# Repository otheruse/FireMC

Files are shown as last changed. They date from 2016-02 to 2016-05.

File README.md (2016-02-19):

 This is FireMC, a motion controller for RepRap 3D printers and Factory Robots like FirePick delta and others. FireMC is currently implemented as an Arduino Due add-on board. FireMC features:
- 12-30V input
- Separate heatbed input
- 12v 1.5A switching regulator for 12v peripherals (if input is not 12v)
- 7 pwm channels (1 heatbed, 3 high power, 1 med power and 2 channels connected to the 12v rail)
- Sockets for 6 stepper drivers
- micro-sd socket
- WiFi via esp8266 module
- 5 thermistor inputs
- 7 limit switch inputs
- 4 io's which can be used for thermocouple inputs and/or servos
- 2 expansion headers for LCD or other peripherals

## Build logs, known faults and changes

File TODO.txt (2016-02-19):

+ Input caps SMPS need 1206 footprint
+ R42 should not be 4K7 (probably 470R-1K)
+ Some motor connectors are too close to 100uF caps
+ Need a smaller inductor for SMPS
- Print info on silkscreen 
	+ jumper locations
	+ stepper name
	- stepper orientation
	+ connector name/function/polarity
+ Via's in power tracks should be bigger (or multiple via's)
+ Check if SMPS is working/what is wrong
+ check what we have on d13 - has arduino led on it
- See if it's useful to connect more IO's of the esp8266 to the arduino
+ Check if we can have hardware PWM on some (all?) of the pwm outputs (pwm outputs are d2-d13) -> We now have all except LP-FET2 on pwm outputs
+ Don't use tx0 and rx0, they are connected to the atmega 16u2
+ pin 20 and 21 (sda and scl) have 1k5 pull-ups: check what's connected to them! -> Now: eeprom
+ is the led on a high-current pin? -> No. Is on the same pin as arduino led
+ Add header for I2C (sda, scl and gnd)
+ Add 5v, GND, SIG for Karl

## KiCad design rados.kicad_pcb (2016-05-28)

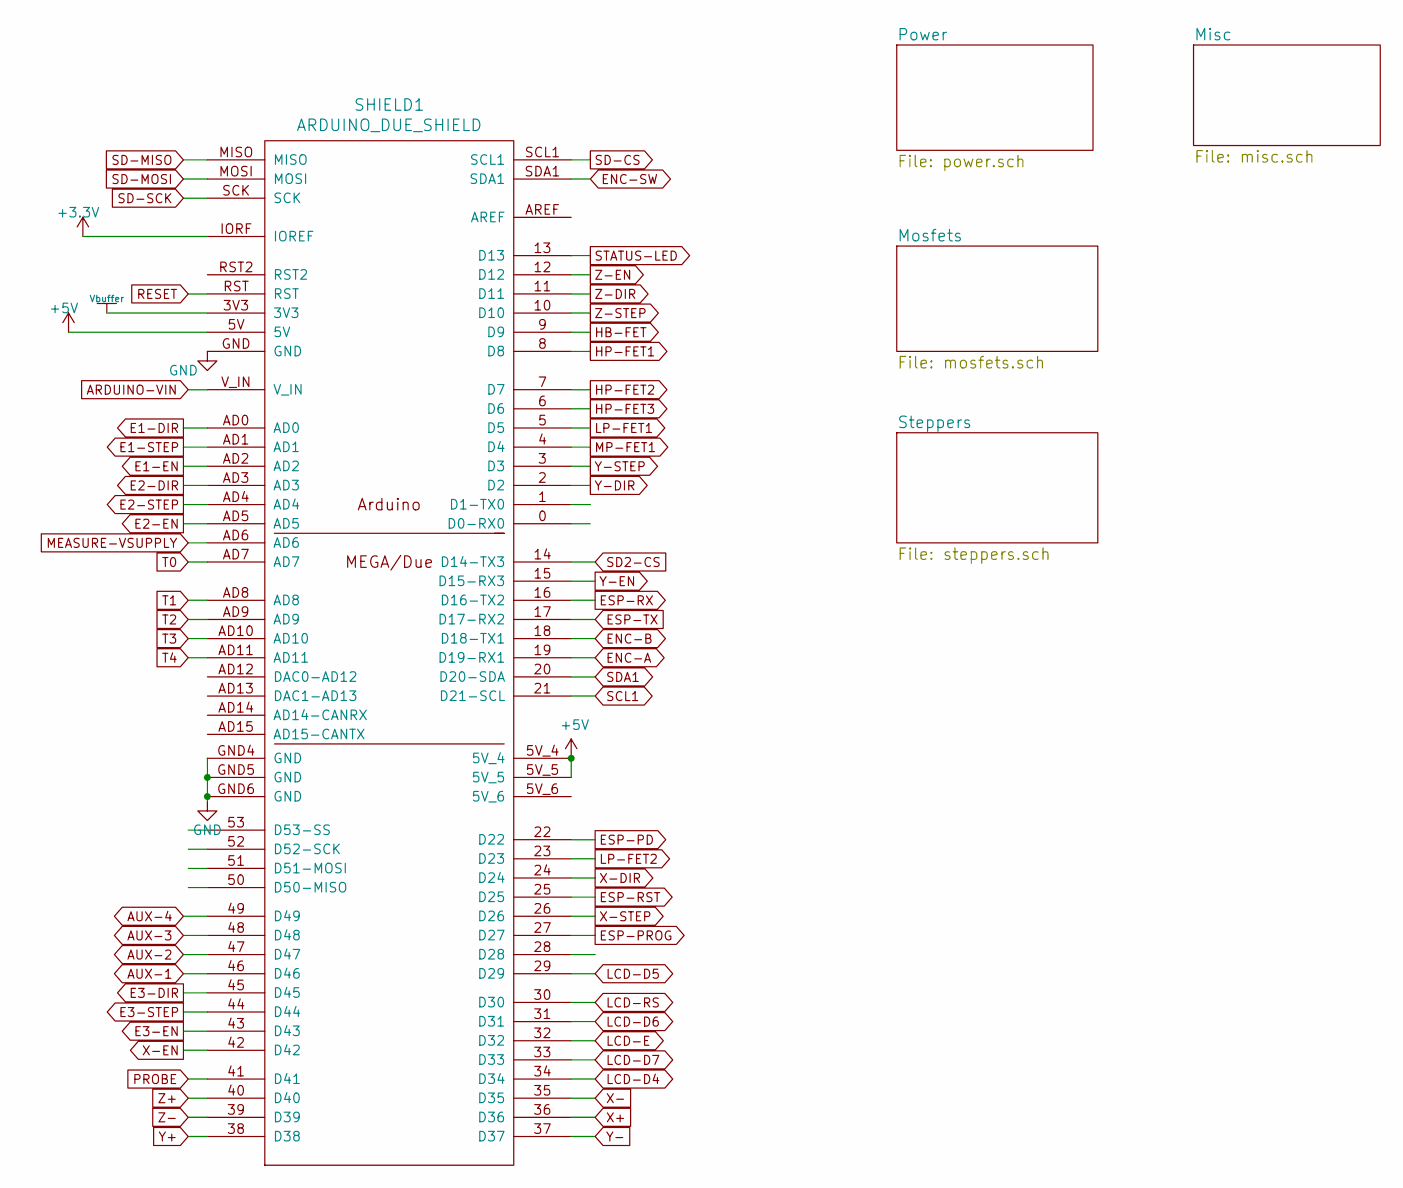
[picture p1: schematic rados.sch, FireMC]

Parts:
SHIELD1: ARDUINO_DUE_SHIELD; ARDUINO_MEGA_DUE_SHIELD_FOOTPRINT_OTH2

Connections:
+5V: SHIELD1.5V, SHIELD1.5V_4, SHIELD1.5V_5; also elsewhere on the board
ARDUINO-VIN: SHIELD1.V_IN; also elsewhere on the board
AUX-1: SHIELD1.46 (D46); also elsewhere on the board
AUX-2: SHIELD1.47 (D47); also elsewhere on the board
AUX-3: SHIELD1.48 (D48); also elsewhere on the board
AUX-4: SHIELD1.49 (D49); also elsewhere on the board
E1-DIR: SHIELD1.AD0; also elsewhere on the board
E1-EN: SHIELD1.AD2; also elsewhere on the board
E1-STEP: SHIELD1.AD1; also elsewhere on the board
E2-DIR: SHIELD1.AD3; also elsewhere on the board
E2-EN: SHIELD1.AD5; also elsewhere on the board
E2-STEP: SHIELD1.AD4; also elsewhere on the board
E3-DIR: SHIELD1.45 (D45); also elsewhere on the board
E3-EN: SHIELD1.43 (D43); also elsewhere on the board
E3-STEP: SHIELD1.44 (D44); also elsewhere on the board
ENC-A: SHIELD1.19 (D19-RX1); also elsewhere on the board
ENC-B: SHIELD1.18 (D18-TX1); also elsewhere on the board
ENC-SW: SHIELD1.SDA1; also elsewhere on the board
ESP-PD: SHIELD1.22 (D22); also elsewhere on the board
ESP-PROG: SHIELD1.27 (D27); also elsewhere on the board
ESP-RST: SHIELD1.25 (D25); also elsewhere on the board
ESP-RX: SHIELD1.16 (D16-TX2); also elsewhere on the board
ESP-TX: SHIELD1.17 (D17-RX2); also elsewhere on the board
GND: SHIELD1.GND, SHIELD1.GND4 (GND), SHIELD1.GND5 (GND), SHIELD1.GND6 (GND); also elsewhere on the board
HB-FET: SHIELD1.9 (D9); also elsewhere on the board
HP-FET1: SHIELD1.8 (D8); also elsewhere on the board
HP-FET2: SHIELD1.7 (D7); also elsewhere on the board
HP-FET3: SHIELD1.6 (D6); also elsewhere on the board
LCD-D4: SHIELD1.34 (D34); also elsewhere on the board
LCD-D5: SHIELD1.29 (D29); also elsewhere on the board
LCD-D6: SHIELD1.31 (D31); also elsewhere on the board
LCD-D7: SHIELD1.33 (D33); also elsewhere on the board
LCD-E: SHIELD1.32 (D32); also elsewhere on the board
LCD-RS: SHIELD1.30 (D30); also elsewhere on the board
LP-FET1: SHIELD1.5 (D5); also elsewhere on the board
LP-FET2: SHIELD1.23 (D23); also elsewhere on the board
MEASURE-VSUPPLY: SHIELD1.AD6; also elsewhere on the board
MP-FET1: SHIELD1.4 (D4); also elsewhere on the board
PROBE: SHIELD1.41 (D41); also elsewhere on the board
RESET: SHIELD1.RST; also elsewhere on the board
SCL1: SHIELD1.21 (D21-SCL); also elsewhere on the board
SD2-CS: SHIELD1.14 (D14-TX3); also elsewhere on the board
SD-CS: SHIELD1.SCL1; also elsewhere on the board
SD-MISO: SHIELD1.MISO; also elsewhere on the board
SD-MOSI: SHIELD1.MOSI; also elsewhere on the board
SD-SCK: SHIELD1.SCK; also elsewhere on the board
SDA1: SHIELD1.20 (D20-SDA); also elsewhere on the board
STATUS-LED: SHIELD1.13 (D13); also elsewhere on the board
T0: SHIELD1.AD7; also elsewhere on the board
T1: SHIELD1.AD8; also elsewhere on the board
T2: SHIELD1.AD9; also elsewhere on the board
T3: SHIELD1.AD10; also elsewhere on the board
T4: SHIELD1.AD11; also elsewhere on the board
Vbuffer: SHIELD1.3V3
X+: SHIELD1.36 (D36); also elsewhere on the board
X-: SHIELD1.35 (D35); also elsewhere on the board
X-DIR: SHIELD1.24 (D24); also elsewhere on the board
X-EN: SHIELD1.42 (D42); also elsewhere on the board
X-STEP: SHIELD1.26 (D26); also elsewhere on the board
Y+: SHIELD1.38 (D38); also elsewhere on the board
Y-: SHIELD1.37 (D37); also elsewhere on the board
Y-DIR: SHIELD1.2 (D2); also elsewhere on the board
Y-EN: SHIELD1.15 (D15-RX3); also elsewhere on the board
Y-STEP: SHIELD1.3 (D3); also elsewhere on the board
Z+: SHIELD1.40 (D40); also elsewhere on the board
Z-: SHIELD1.39 (D39); also elsewhere on the board
Z-DIR: SHIELD1.11 (D11); also elsewhere on the board
Z-EN: SHIELD1.12 (D12); also elsewhere on the board
Z-STEP: SHIELD1.10 (D10); also elsewhere on the board

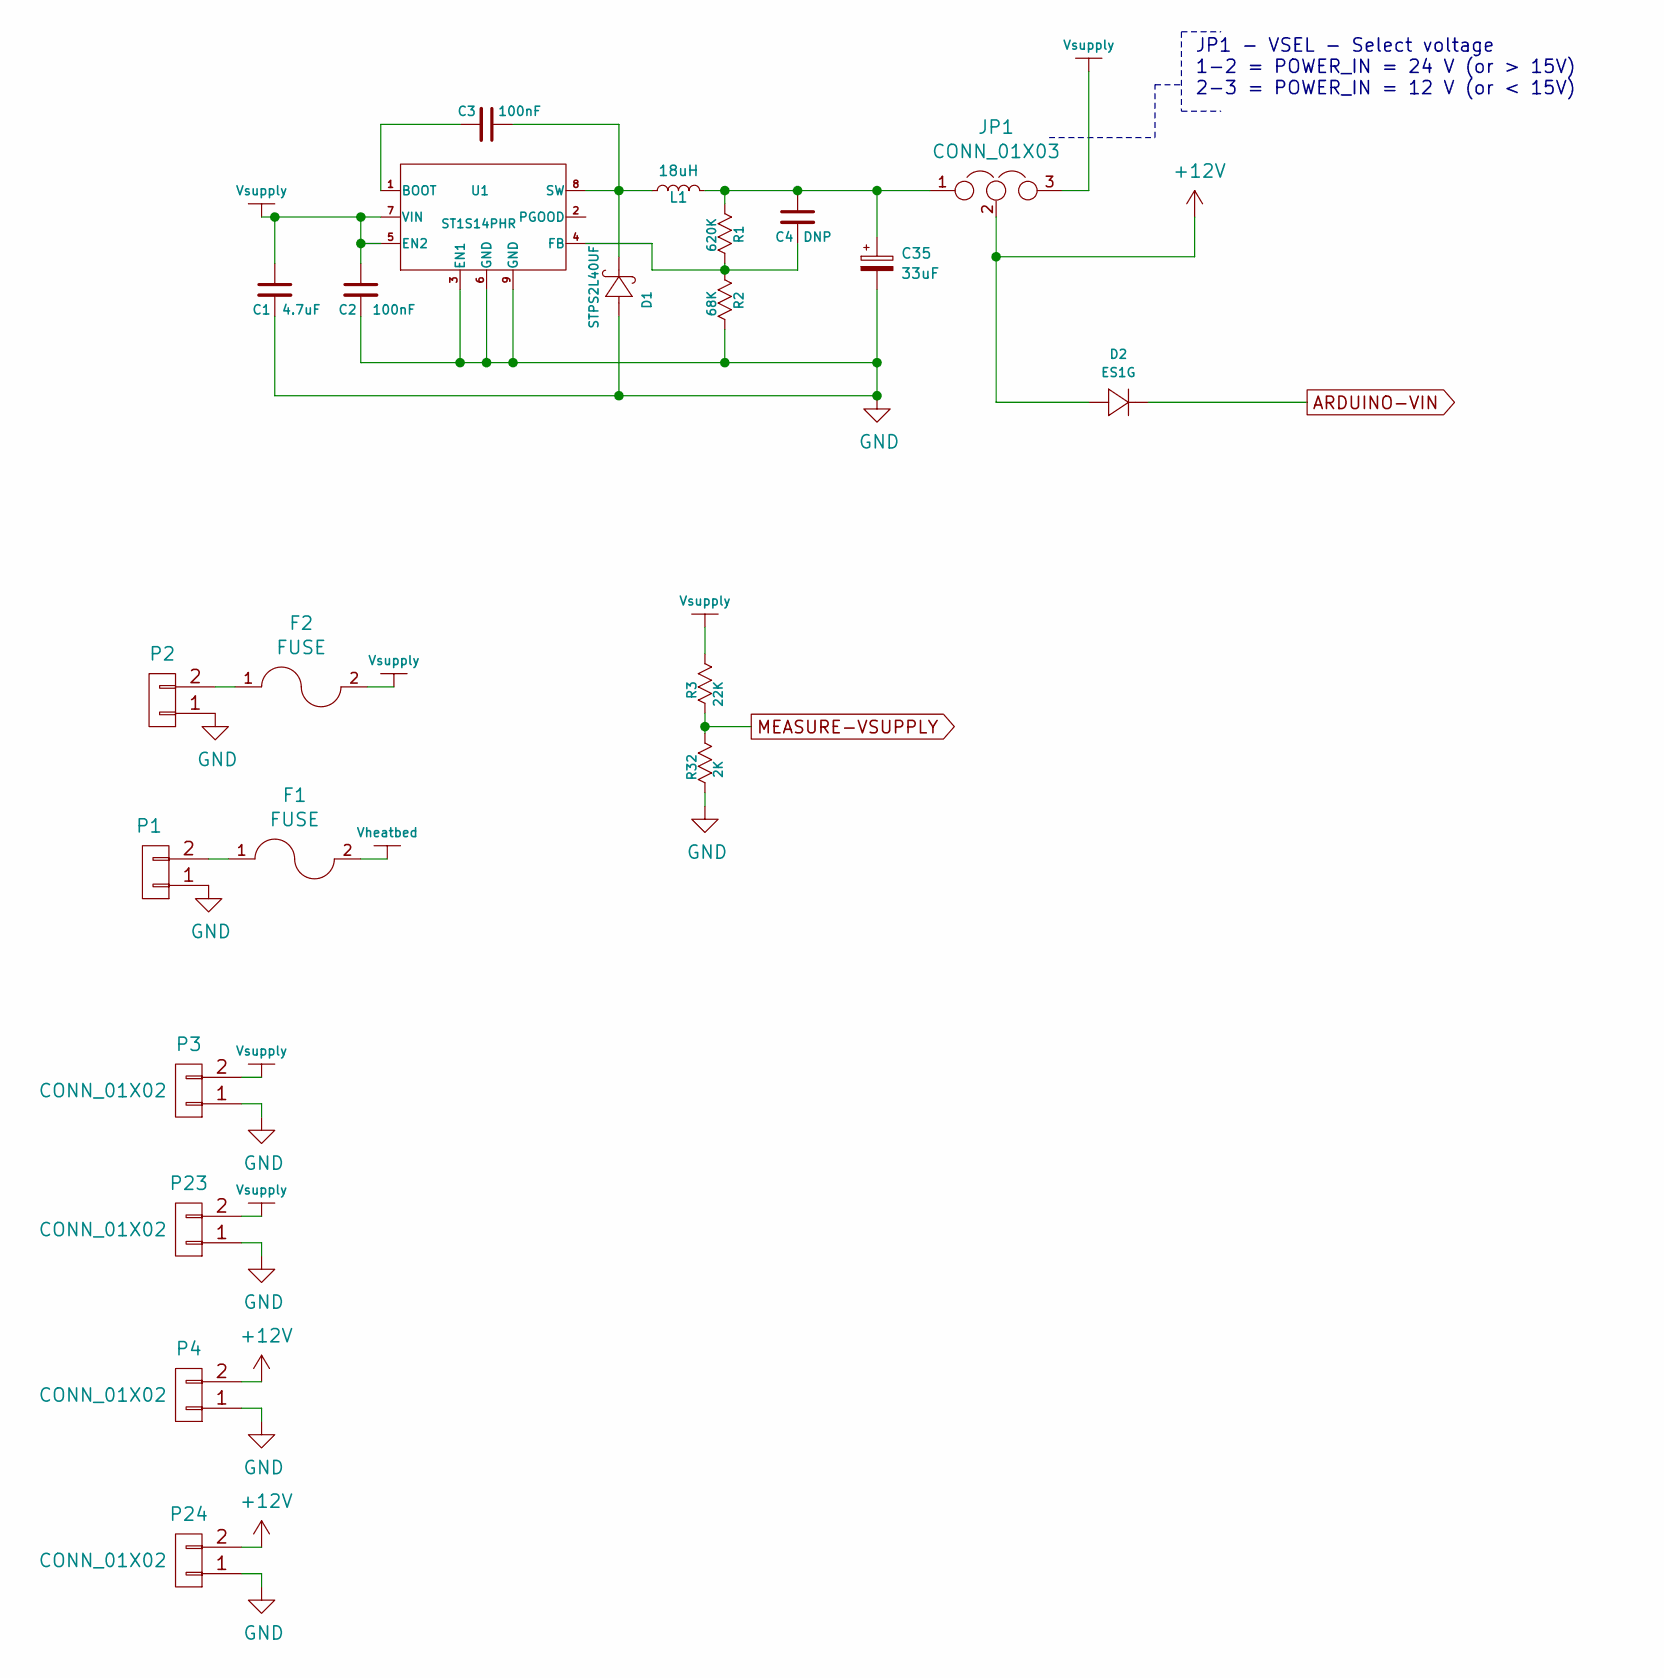
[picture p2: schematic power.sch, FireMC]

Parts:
C1: 4.7uF; C_1210; VoltageRating 50V
C2, C3: 100nF; C_0603; VoltageRating 50V
C4: DNP; C_0603
C35: 33uF; c_elec_6.3x7.7; VoltageRating 25V
D1: STPS2L40UF; DO214AA_SMB
D2: ES1G; DO214AC_SMA
F1, F2: FUSE; FUSEHOLDER_MINI_KEYSTONE_3557
JP1: CONN_01X03; CON_HDR_1x3_2.54mm
L1: 18uH; INDUCTOR_BOURNS_RLB914
P1, P2: CONN_01X02; CON_PHOENIX_MSTBA-2.5-2-G-5.08
P3, P4, P23, P24: CONN_01X02; CON_HDR_1x2_2.54mm
R1: 620K; R_0603
R2: 68K; R_0603
R3: 22K; R_0603
R32: 2K; R_0603
U1: ST1S14PHR; HSOP8

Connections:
+12V: D2.2, JP1.2, P4.2, P24.2; also elsewhere on the board
GND: C1.2, C2.2, C35.2, D1.2 (anode), P1.1, P2.1, P3.1, P4.1, P23.1, P24.1, R2.2, R32.2, U1.3 (EN1), U1.6 (GND), U1.9 (GND); also elsewhere on the board
MEASURE-VSUPPLY: R3.2, R32.1; also elsewhere on the board
unnamed: C3.1, D1.1 (cathode), L1.1, U1.8 (SW)
unnamed: C3.2, U1.1 (BOOT)
unnamed: C4.2, R1.2, R2.1, U1.4 (FB)
unnamed: C4.1, C35.1, JP1.1, L1.2, R1.1
unnamed 50: D2.1; also elsewhere on the board
unnamed: F1.1, P1.2
unnamed: F2.1, P2.2
Vheatbed: F1.2; also elsewhere on the board
Vsupply: C1.1, C2.1, F2.2, JP1.3, P3.2, P23.2, R3.1, U1.5 (EN2), U1.7 (VIN); also elsewhere on the board

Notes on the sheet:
JP1 - VSEL - Select voltage 1-2 = POWER_IN = 24 V (or > 15V) 2-3 = POWER_IN = 12 V (or < 15V)

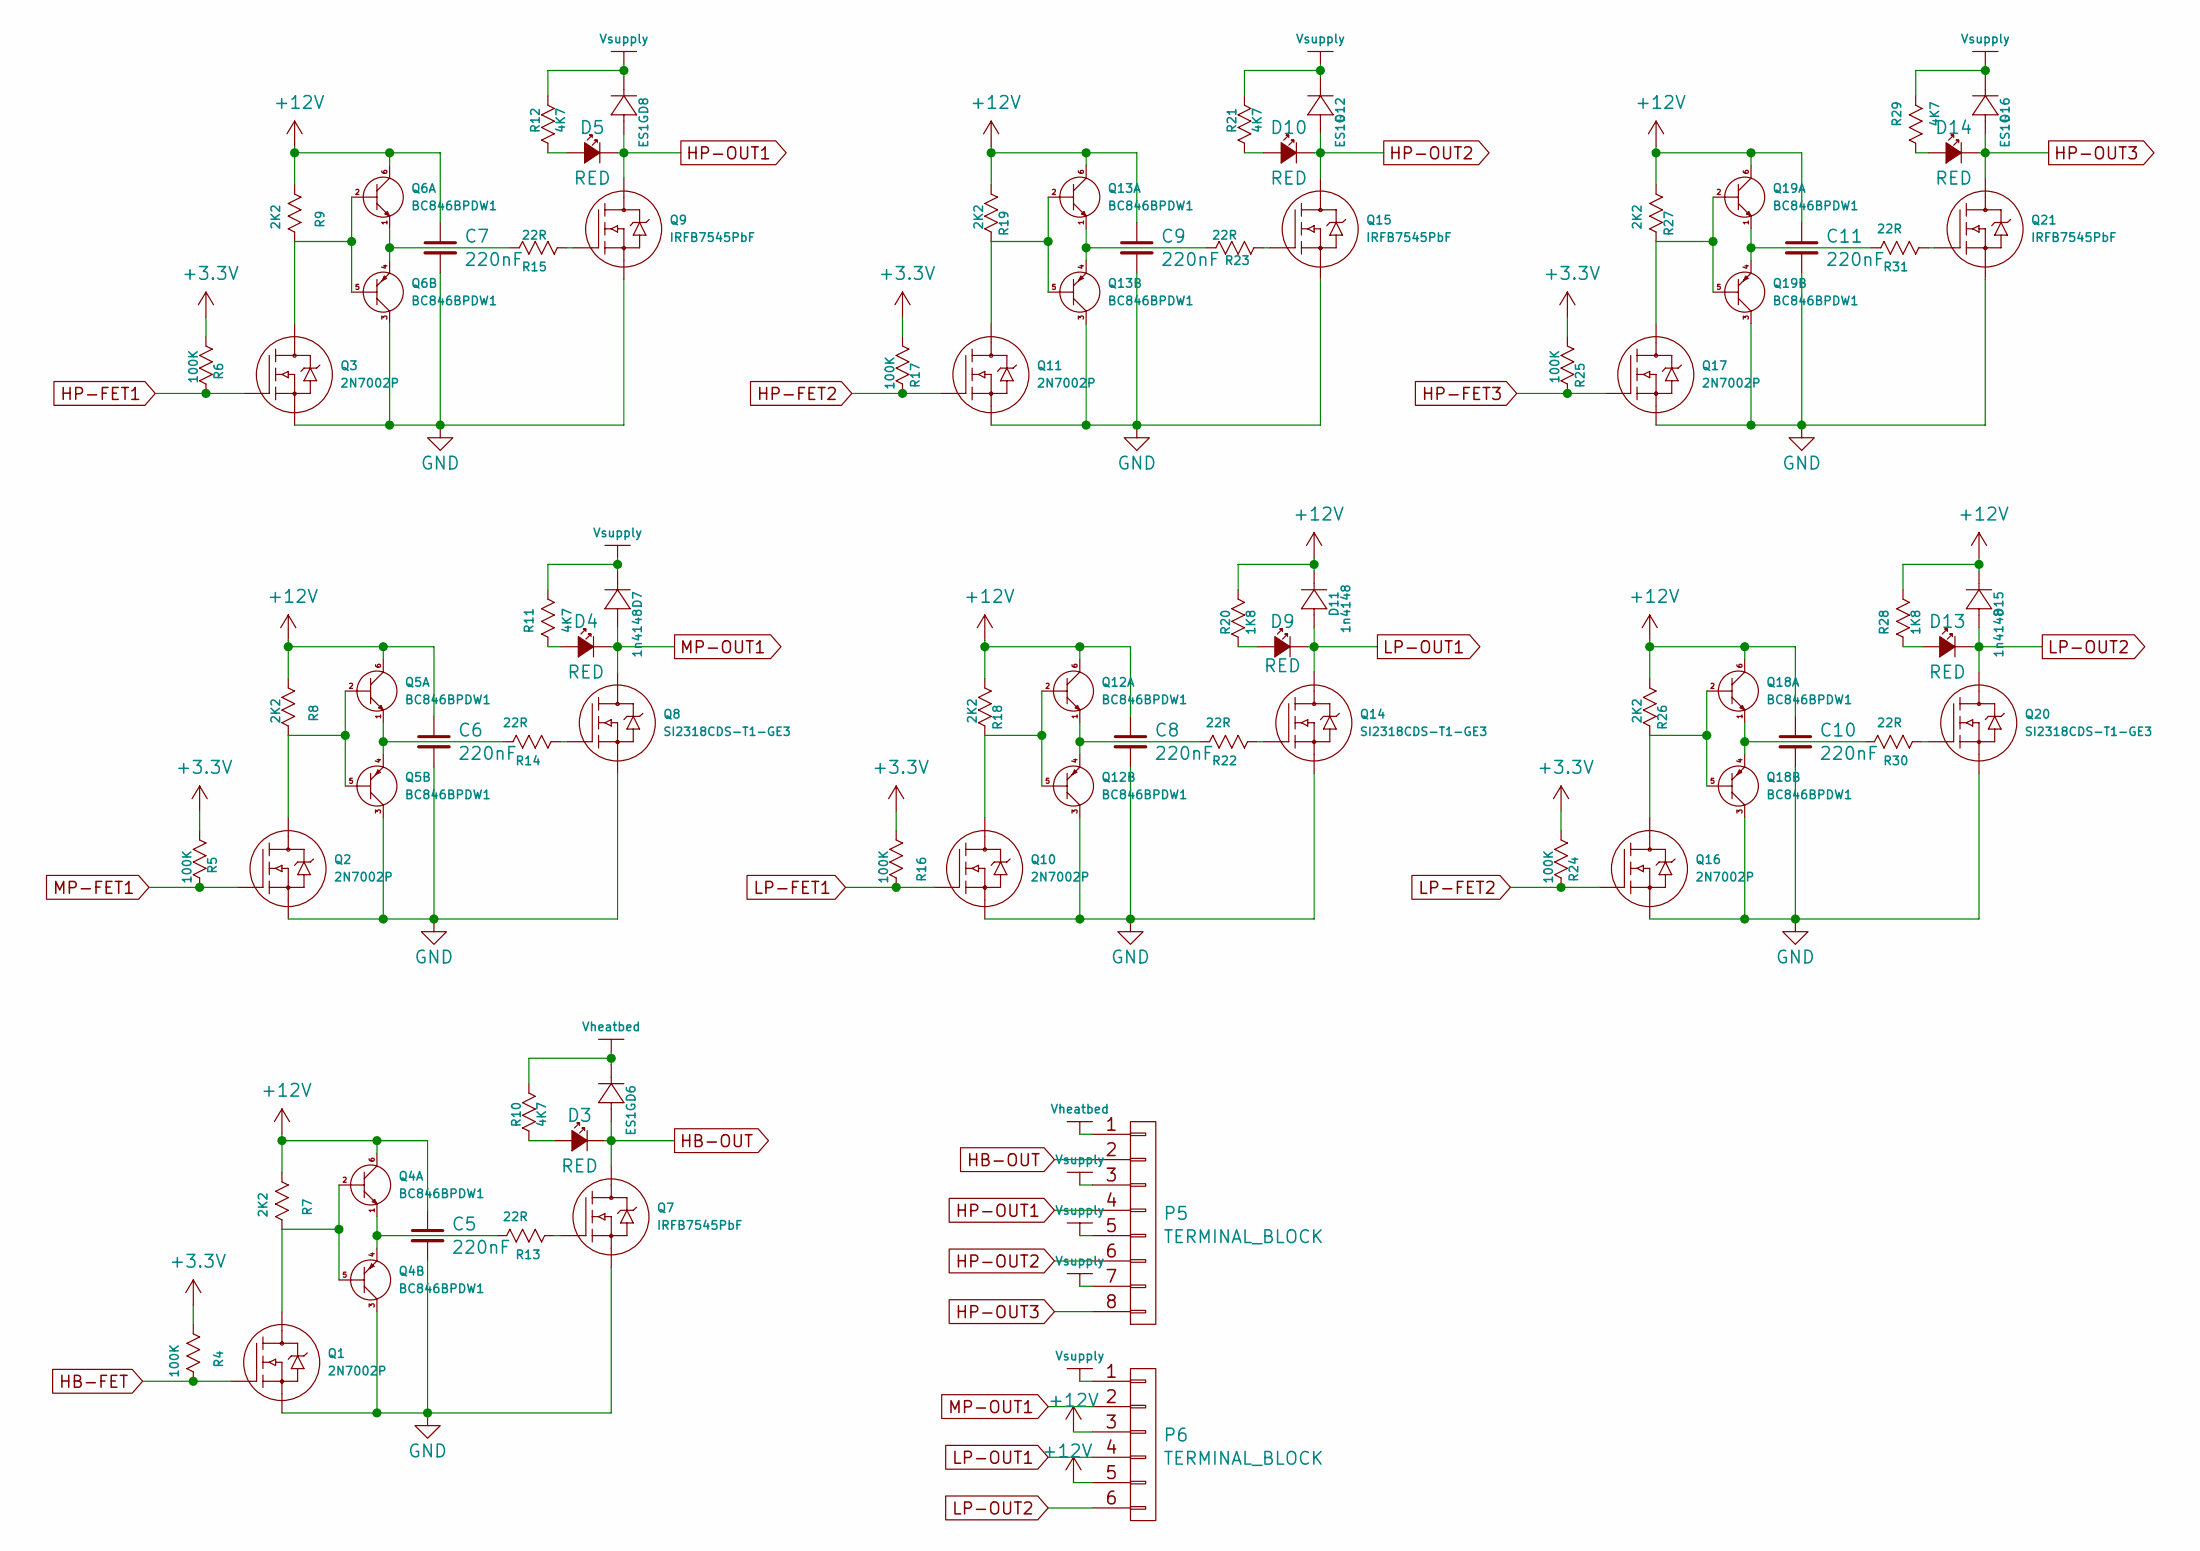
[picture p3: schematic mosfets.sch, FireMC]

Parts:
C5, C6, C7, C8, C9, C10, C11: 220nF; C_0603; VoltageRating 16V
D3, D4, D5, D9, D10, D13, D14: RED; LED-0603
D6, D8, D12, D16: ES1G; DO214AC_SMA
D7, D11, D15: 1n4148; DO213AA_SOD-80_MiniMelf
P5: TERMINAL_BLOCK; TERMINAL_BLOCK_8_PIN_5mm
P6: TERMINAL_BLOCK; TERMINAL_BLOCK_6_PIN_5mm
Q1, Q2, Q3, Q10, Q11, Q16, Q17: 2N7002P; SOT23_3L
Q4, Q5, Q6, Q12, Q13, Q18, Q19: BC846BPDW1; SC70_6L
Q7, Q9, Q15, Q21: IRFB7545PbF; TO-220-3
Q8, Q14, Q20: SI2318CDS-T1-GE3; SOT23_3L
R4, R5, R6, R16, R17, R24, R25: 100K; R_0603
R7, R8, R9, R18, R19, R26, R27: 2K2; R_0603
R10, R11, R12, R21, R29: 4K7; R_0805
R13, R14, R15, R22, R23, R30, R31: 22R; R_0603
R20, R28: 1K8; R_0603

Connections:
+12V: C5.1, C6.1, C7.1, C8.1, C9.1, C10.1, C11.1, D11.2, D15.2, P6.3, P6.5, Q4.6 (C), Q5.6 (C), Q6.6 (C), Q12.6 (C), Q13.6 (C), Q18.6 (C), Q19.6 (C), R7.2, R8.2, R9.2, R18.2, R19.2, R20.1, R26.2, R27.2, R28.1; also elsewhere on the board
GND: C5.2, C6.2, C7.2, C8.2, C9.2, C10.2, C11.2, Q1.2 (S), Q2.2 (S), Q3.2 (S), Q4.3 (C), Q5.3 (C), Q6.3 (C), Q7.3 (S), Q8.2 (S), Q9.3 (S), Q10.2 (S), Q11.2 (S), Q12.3 (C), Q13.3 (C), Q14.2 (S), Q15.3 (S), Q16.2 (S), Q17.2 (S), Q18.3 (C), Q19.3 (C), Q20.2 (S), Q21.3 (S); also elsewhere on the board
HB-FET: Q1.1 (G), R4.1; also elsewhere on the board
HB-OUT: D3.2 (K), D6.2, P5.2, Q7.2 (D)
HP-FET1: Q3.1 (G), R6.1; also elsewhere on the board
HP-FET2: Q11.1 (G), R17.1; also elsewhere on the board
HP-FET3: Q17.1 (G), R25.1; also elsewhere on the board
HP-OUT1: D5.2 (K), D8.2, P5.4, Q9.2 (D)
HP-OUT2: D10.2 (K), D12.2, P5.6, Q15.2 (D)
HP-OUT3: D14.2 (K), D16.2, P5.8, Q21.2 (D)
LP-FET1: Q10.1 (G), R16.1; also elsewhere on the board
LP-FET2: Q16.1 (G), R24.1; also elsewhere on the board
LP-OUT1: D9.2 (K), D11.1, P6.4, Q14.3 (D)
LP-OUT2: D13.2 (K), D15.1, P6.6, Q20.3 (D)
MP-FET1: Q2.1 (G), R5.1; also elsewhere on the board
MP-OUT1: D4.2 (K), D7.1, P6.2, Q8.3 (D)
unnamed: D3.1 (A), R10.2
unnamed: D4.1 (A), R11.2
unnamed: D5.1 (A), R12.2
unnamed: D9.1 (A), R20.2
unnamed: D10.1 (A), R21.2
unnamed: D13.1 (A), R28.2
unnamed: D14.1 (A), R29.2
unnamed: Q1.3 (D), Q4.2 (B), Q4.5 (B), R7.1
unnamed: Q2.3 (D), Q5.2 (B), Q5.5 (B), R8.1
unnamed: Q3.3 (D), Q6.2 (B), Q6.5 (B), R9.1
unnamed: Q4.1 (E), Q4.4 (E), R13.1
unnamed: Q5.1 (E), Q5.4 (E), R14.1
unnamed: Q6.1 (E), Q6.4 (E), R15.1
unnamed: Q7.1 (G), R13.2
unnamed: Q8.1 (G), R14.2
unnamed: Q9.1 (G), R15.2
unnamed: Q10.3 (D), Q12.2 (B), Q12.5 (B), R18.1
unnamed: Q11.3 (D), Q13.2 (B), Q13.5 (B), R19.1
unnamed: Q12.1 (E), Q12.4 (E), R22.1
unnamed: Q13.1 (E), Q13.4 (E), R23.1
unnamed: Q14.1 (G), R22.2
unnamed: Q15.1 (G), R23.2
unnamed: Q16.3 (D), Q18.2 (B), Q18.5 (B), R26.1
unnamed: Q17.3 (D), Q19.2 (B), Q19.5 (B), R27.1
unnamed: Q18.1 (E), Q18.4 (E), R30.1
unnamed: Q19.1 (E), Q19.4 (E), R31.1
unnamed: Q20.1 (G), R30.2
unnamed: Q21.1 (G), R31.2
Vheatbed: D6.1, P5.1, R10.1; also elsewhere on the board
Vsupply: D7.2, D8.1, D12.1, D16.1, P5.3, P5.5, P5.7, P6.1, R11.1, R12.1, R21.1, R29.1; also elsewhere on the board

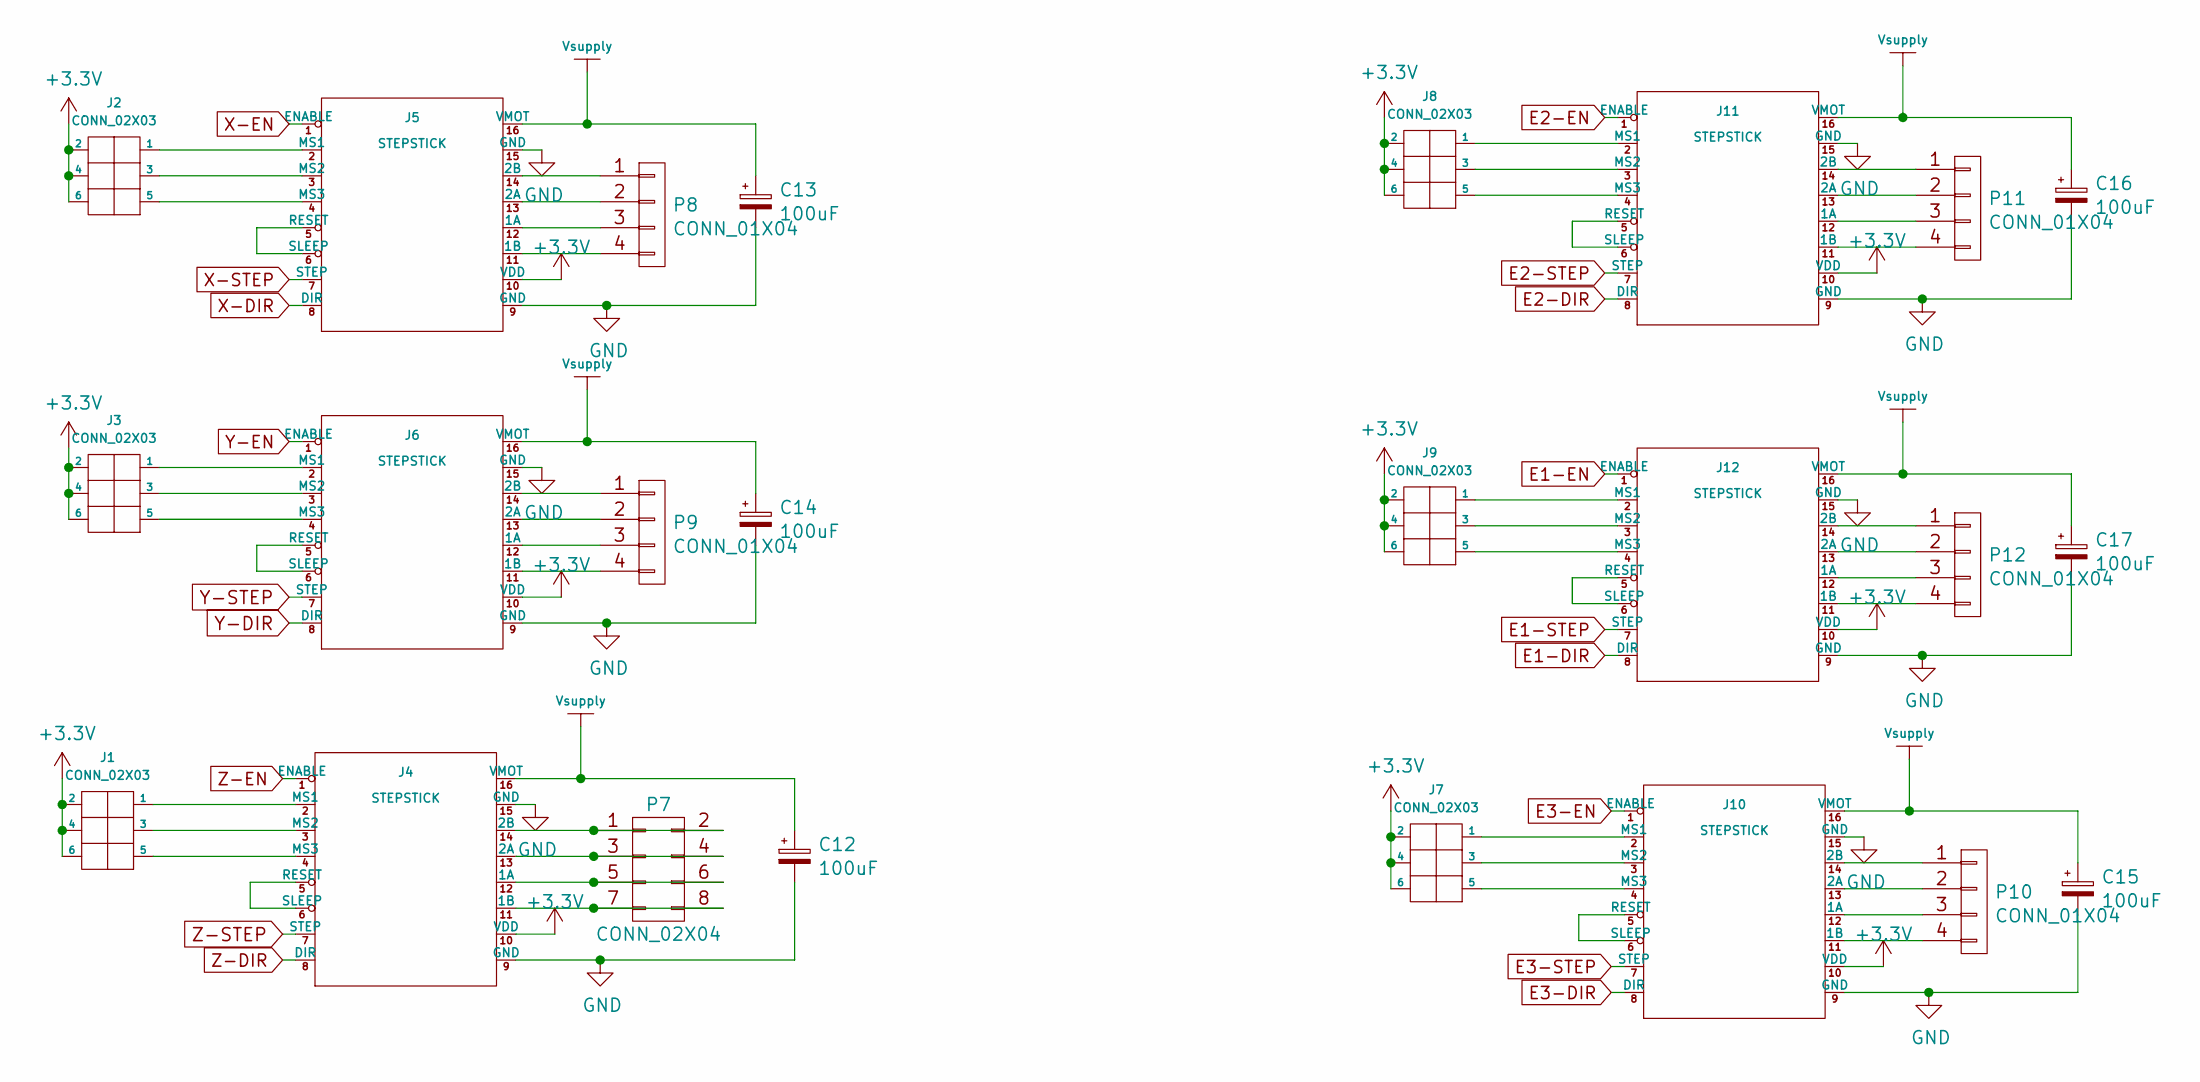
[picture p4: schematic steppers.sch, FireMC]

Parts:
C12, C13, C14, C15, C16, C17: 100uF; c_elec_6.3x7.7; VoltageRating 50V
J1, J2, J3, J7, J8, J9: CONN_02X03; CON_HDR_2x3_2.54mm
J4, J5, J6, J10, J11, J12: STEPSTICK
P7: CONN_02X04; CON_HDR_2x4_2.54mm
P8, P9, P10, P11, P12: CONN_01X04; CON_HDR_1x4_2.54mm

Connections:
E1-DIR: J12.8 (DIR); also elsewhere on the board
E1-EN: J12.1 (ENABLE); also elsewhere on the board
E1-STEP: J12.7 (STEP); also elsewhere on the board
E2-DIR: J11.8 (DIR); also elsewhere on the board
E2-EN: J11.1 (ENABLE); also elsewhere on the board
E2-STEP: J11.7 (STEP); also elsewhere on the board
E3-DIR: J10.8 (DIR); also elsewhere on the board
E3-EN: J10.1 (ENABLE); also elsewhere on the board
E3-STEP: J10.7 (STEP); also elsewhere on the board
GND: C12.2, C13.2, C14.2, C15.2, C16.2, C17.2, J4.9 (GND), J4.15 (GND), J5.9 (GND), J5.15 (GND), J6.9 (GND), J6.15 (GND), J10.9 (GND), J10.15 (GND), J11.9 (GND), J11.15 (GND), J12.9 (GND), J12.15 (GND); also elsewhere on the board
unnamed: J1.1, J4.2 (MS1)
unnamed: J1.3, J4.3 (MS2)
unnamed: J1.5, J4.4 (MS3)
unnamed: J2.1, J5.2 (MS1)
unnamed: J2.3, J5.3 (MS2)
unnamed: J2.5, J5.4 (MS3)
unnamed: J3.1, J6.2 (MS1)
unnamed: J3.3, J6.3 (MS2)
unnamed: J3.5, J6.4 (MS3)
unnamed: J4.5 (RESET), J4.6 (SLEEP)
unnamed: J4.11 (1B), P7.7, P7.8
unnamed: J4.12 (1A), P7.5, P7.6
unnamed: J4.13 (2A), P7.3, P7.4
unnamed: J4.14 (2B), P7.1, P7.2
unnamed: J5.5 (RESET), J5.6 (SLEEP)
unnamed: J5.11 (1B), P8.4
unnamed: J5.12 (1A), P8.3
unnamed: J5.13 (2A), P8.2
unnamed: J5.14 (2B), P8.1
unnamed: J6.5 (RESET), J6.6 (SLEEP)
unnamed: J6.11 (1B), P9.4
unnamed: J6.12 (1A), P9.3
unnamed: J6.13 (2A), P9.2
unnamed: J6.14 (2B), P9.1
unnamed: J7.1, J10.2 (MS1)
unnamed: J7.3, J10.3 (MS2)
unnamed: J7.5, J10.4 (MS3)
unnamed: J10.5 (RESET), J10.6 (SLEEP)
unnamed: J10.11 (1B), P10.4
unnamed: J10.12 (1A), P10.3
unnamed: J10.13 (2A), P10.2
unnamed: J10.14 (2B), P10.1
unnamed: J8.1, J11.2 (MS1)
unnamed: J8.3, J11.3 (MS2)
unnamed: J8.5, J11.4 (MS3)
unnamed: J11.5 (RESET), J11.6 (SLEEP)
unnamed: J11.11 (1B), P11.4
unnamed: J11.12 (1A), P11.3
unnamed: J11.13 (2A), P11.2
unnamed: J11.14 (2B), P11.1
unnamed: J9.1, J12.2 (MS1)
unnamed: J9.3, J12.3 (MS2)
unnamed: J9.5, J12.4 (MS3)
unnamed: J12.5 (RESET), J12.6 (SLEEP)
unnamed: J12.11 (1B), P12.4
unnamed: J12.12 (1A), P12.3
unnamed: J12.13 (2A), P12.2
unnamed: J12.14 (2B), P12.1
Vsupply: C12.1, C13.1, C14.1, C15.1, C16.1, C17.1, J4.16 (VMOT), J5.16 (VMOT), J6.16 (VMOT), J10.16 (VMOT), J11.16 (VMOT), J12.16 (VMOT); also elsewhere on the board
X-DIR: J5.8 (DIR); also elsewhere on the board
X-EN: J5.1 (ENABLE); also elsewhere on the board
X-STEP: J5.7 (STEP); also elsewhere on the board
Y-DIR: J6.8 (DIR); also elsewhere on the board
Y-EN: J6.1 (ENABLE); also elsewhere on the board
Y-STEP: J6.7 (STEP); also elsewhere on the board
Z-DIR: J4.8 (DIR); also elsewhere on the board
Z-EN: J4.1 (ENABLE); also elsewhere on the board
Z-STEP: J4.7 (STEP); also elsewhere on the board

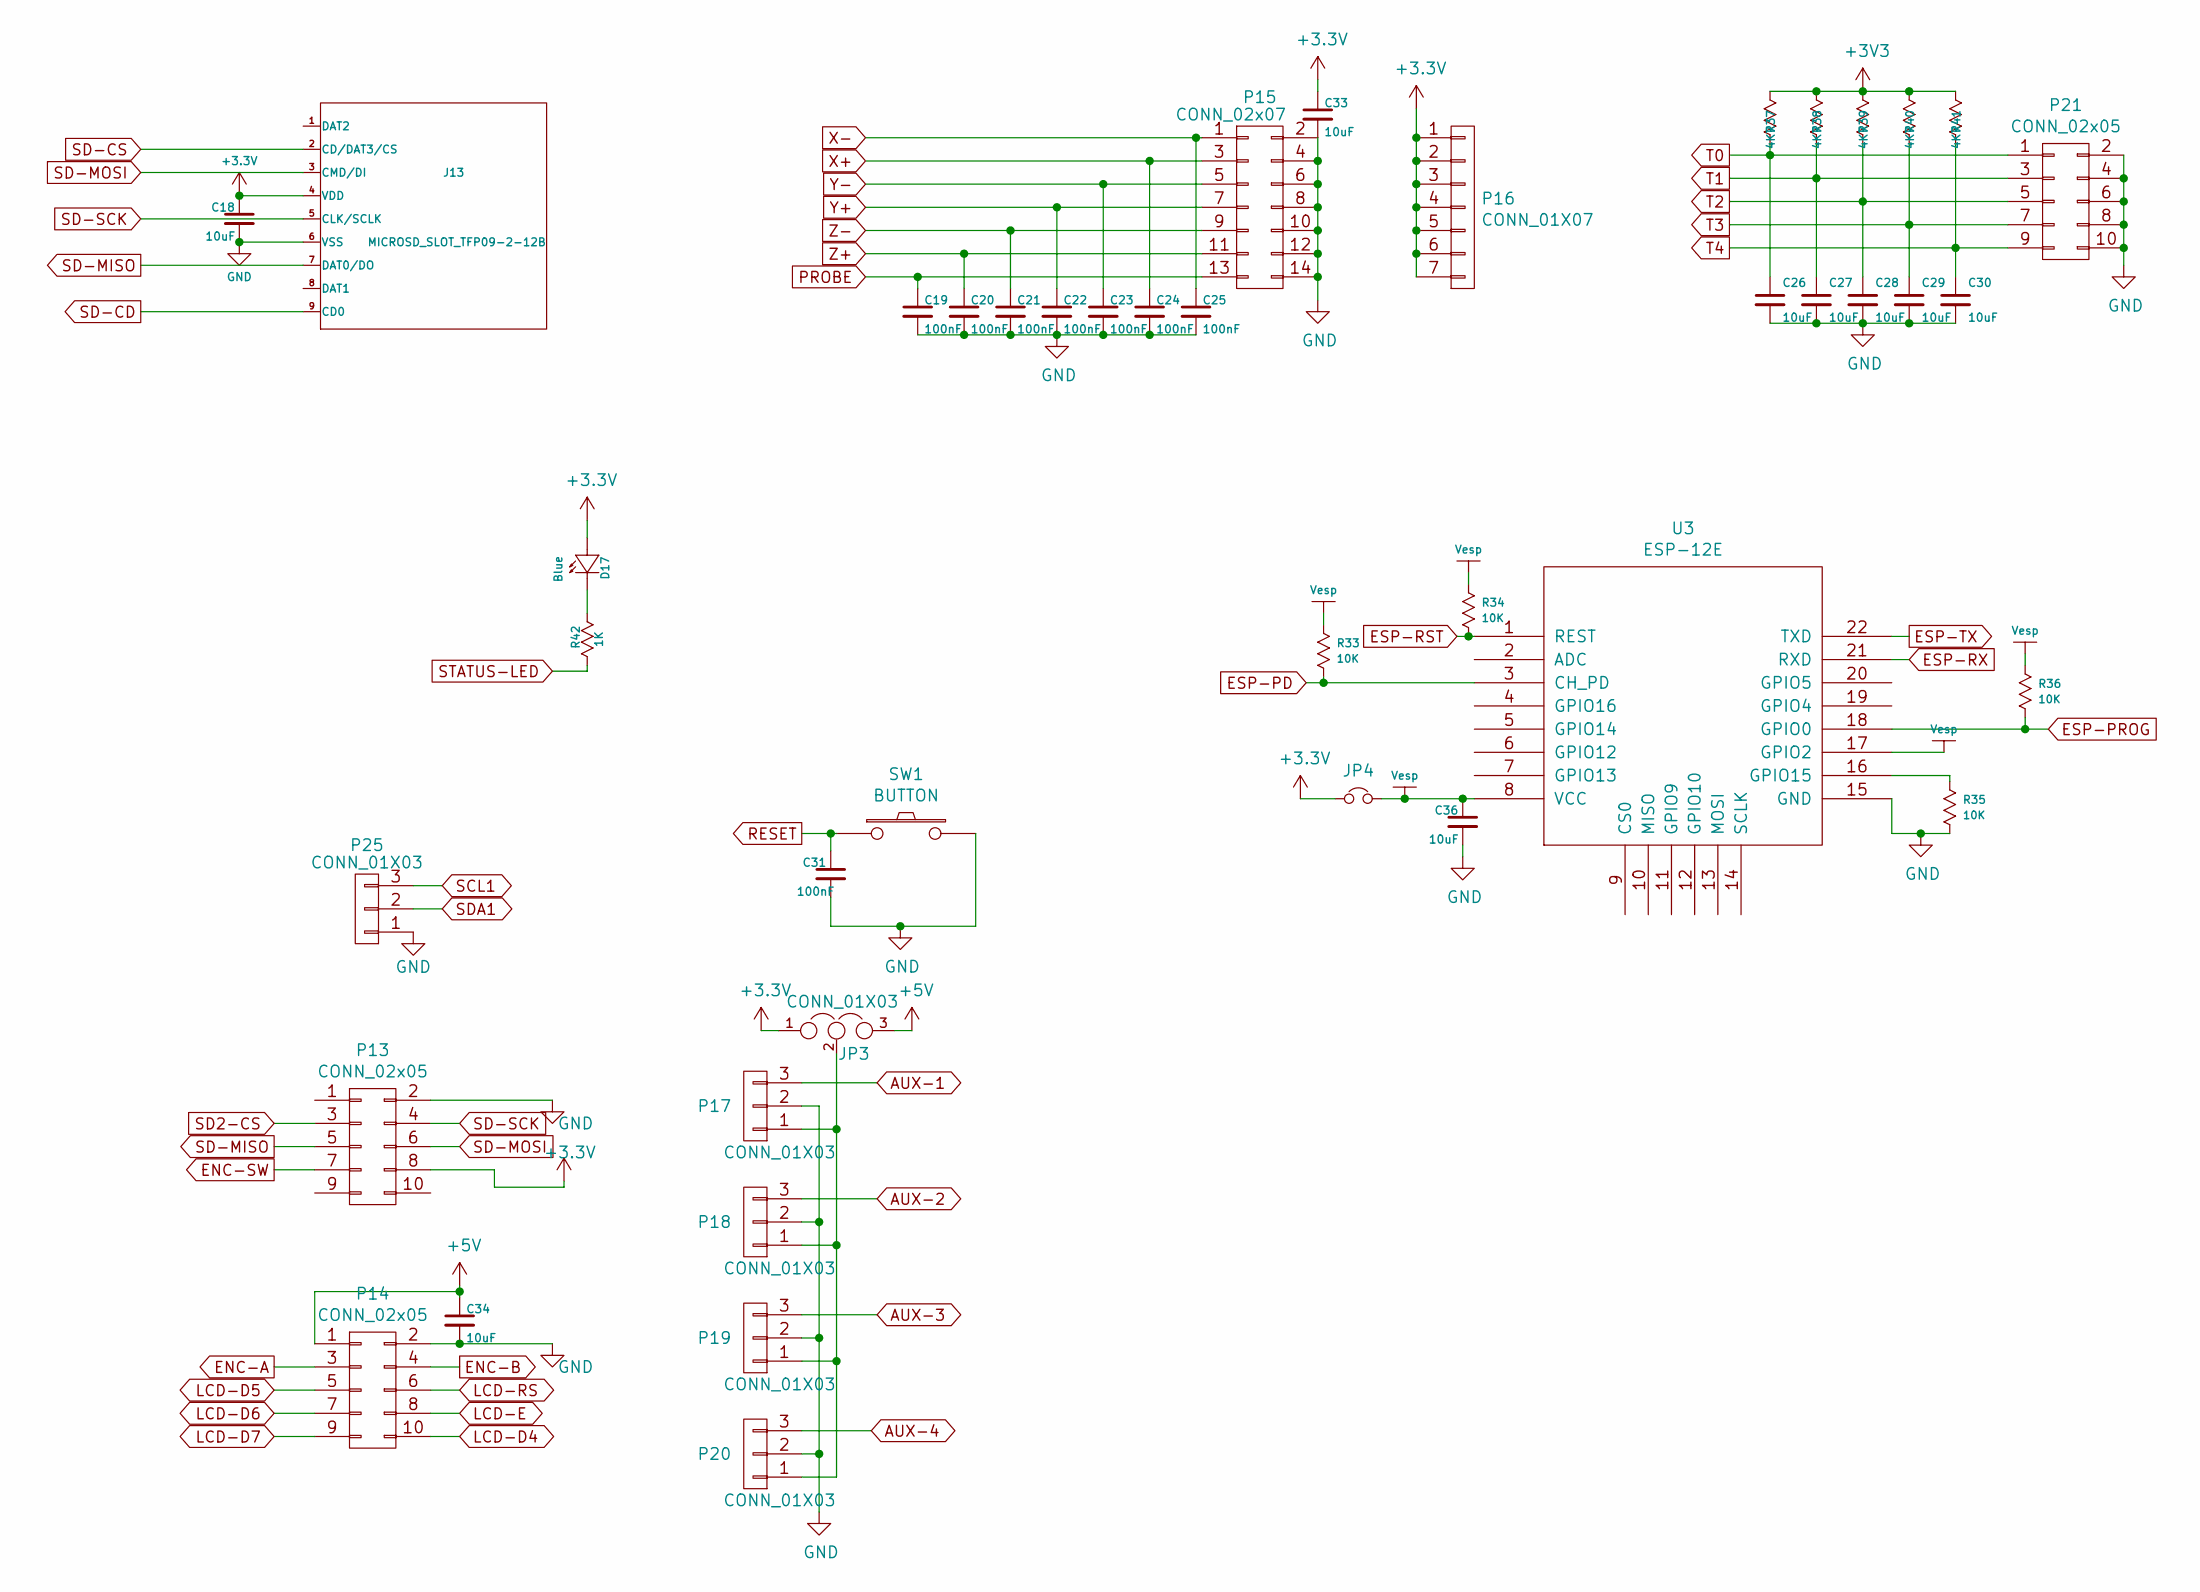
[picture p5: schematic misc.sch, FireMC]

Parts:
C18, C26, C27, C28, C29, C30, C33, C34, C36: 10uF; C_0805; VoltageRating 6.3V
C19, C20, C21, C22, C23, C24, C25, C31: 100nF; C_0603; VoltageRating 16V
D17: Blue; LED-0603
J13: MICROSD_SLOT_TFP09-2-12B
JP3: CONN_01X03; CON_HDR_1x3_2.54mm
JP4: CONN_01X02; CON_HDR_1x2_2.54mm
P13, P14, P21: CONN_02x05; CON_HDR_2x5_2.54mm
P15: CONN_02x07; CON_HDR_2x7_2.54mm
P16: CONN_01X07; CON_HDR_1x7_2.54mm
P17, P18, P19, P20, P25: CONN_01X03; CON_HDR_1x3_2.54mm
R33, R34, R35, R36: 10K; R_0603
R37, R38, R39, R40, R41: 4K7; R_0603
R42: 1K; R_0603
SW1: BUTTON; BUTTON_PUSH_SMD_6x6mm
U3: ESP-12E

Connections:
+5V: C34.1, JP3.3, P14.1; also elsewhere on the board
AUX-1: P17.3; also elsewhere on the board
AUX-2: P18.3; also elsewhere on the board
AUX-3: P19.3; also elsewhere on the board
AUX-4: P20.3; also elsewhere on the board
ENC-A: P14.3; also elsewhere on the board
ENC-B: P14.4; also elsewhere on the board
ENC-SW: P13.7; also elsewhere on the board
ESP-PD: R33.2, U3.3 (CH_PD); also elsewhere on the board
ESP-PROG: R36.2, U3.18 (GPIO0); also elsewhere on the board
ESP-RST: R34.2, U3.1 (REST); also elsewhere on the board
ESP-RX: U3.21 (RXD); also elsewhere on the board
ESP-TX: U3.22 (TXD); also elsewhere on the board
GND: C18.2, C19.2, C20.2, C21.2, C22.2, C23.2, C24.2, C25.2, C26.2, C27.2, C28.2, C29.2, C30.2, C31.2, C33.2, C34.2, C36.2, J13.6 (VSS), P13.2, P14.2, P15.2, P15.4, P15.6, P15.8, P15.10, P15.12, P15.14, P17.2, P18.2, P19.2, P20.2, P21.2, P21.4, P21.6, P21.8, P21.10, P25.1, R35.2, SW1.2, U3.15 (GND); also elsewhere on the board
LCD-D4: P14.10; also elsewhere on the board
LCD-D5: P14.5; also elsewhere on the board
LCD-D6: P14.7; also elsewhere on the board
LCD-D7: P14.9; also elsewhere on the board
LCD-E: P14.8; also elsewhere on the board
LCD-RS: P14.6; also elsewhere on the board
unnamed: D17.2, R42.1
unnamed: JP3.2, P17.1, P18.1, P19.1, P20.1
unnamed: R35.1, U3.16 (GPIO15)
PROBE: C19.1, P15.13; also elsewhere on the board
RESET: C31.1, SW1.1; also elsewhere on the board
SCL1: P25.3; also elsewhere on the board
SD2-CS: P13.3; also elsewhere on the board
SD-CD: J13.9 (CD0)
SD-CS: J13.2 (CD/DAT3/CS); also elsewhere on the board
SD-MISO: J13.7 (DAT0/DO), P13.5; also elsewhere on the board
SD-MOSI: J13.3 (CMD/DI), P13.6; also elsewhere on the board
SD-SCK: J13.5 (CLK/SCLK), P13.4; also elsewhere on the board
SDA1: P25.2; also elsewhere on the board
STATUS-LED: R42.2; also elsewhere on the board
T0: C26.1, P21.1, R37.2; also elsewhere on the board
T1: C27.1, P21.3, R38.2; also elsewhere on the board
T2: C28.1, P21.5, R39.2; also elsewhere on the board
T3: C29.1, P21.7, R40.2; also elsewhere on the board
T4: C30.1, P21.9, R41.2; also elsewhere on the board
Vesp: C36.1, JP4.2, R33.1, R34.1, R36.1, U3.8 (VCC), U3.17 (GPIO2)
X+: C24.1, P15.3; also elsewhere on the board
X-: C25.1, P15.1; also elsewhere on the board
Y+: C22.1, P15.7; also elsewhere on the board
Y-: C23.1, P15.5; also elsewhere on the board
Z+: C20.1, P15.11; also elsewhere on the board
Z-: C21.1, P15.9; also elsewhere on the board

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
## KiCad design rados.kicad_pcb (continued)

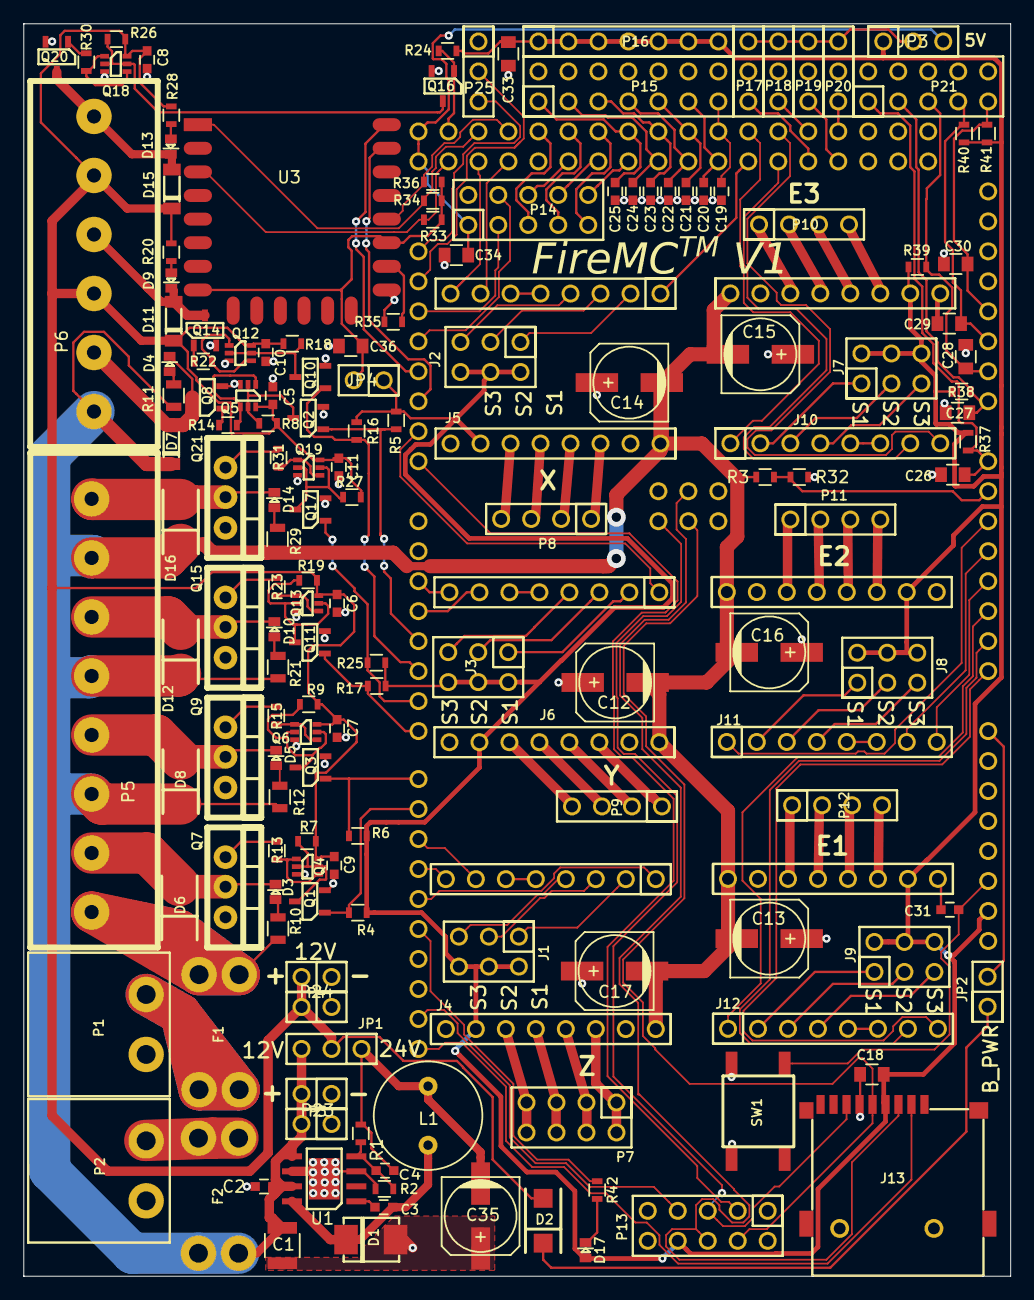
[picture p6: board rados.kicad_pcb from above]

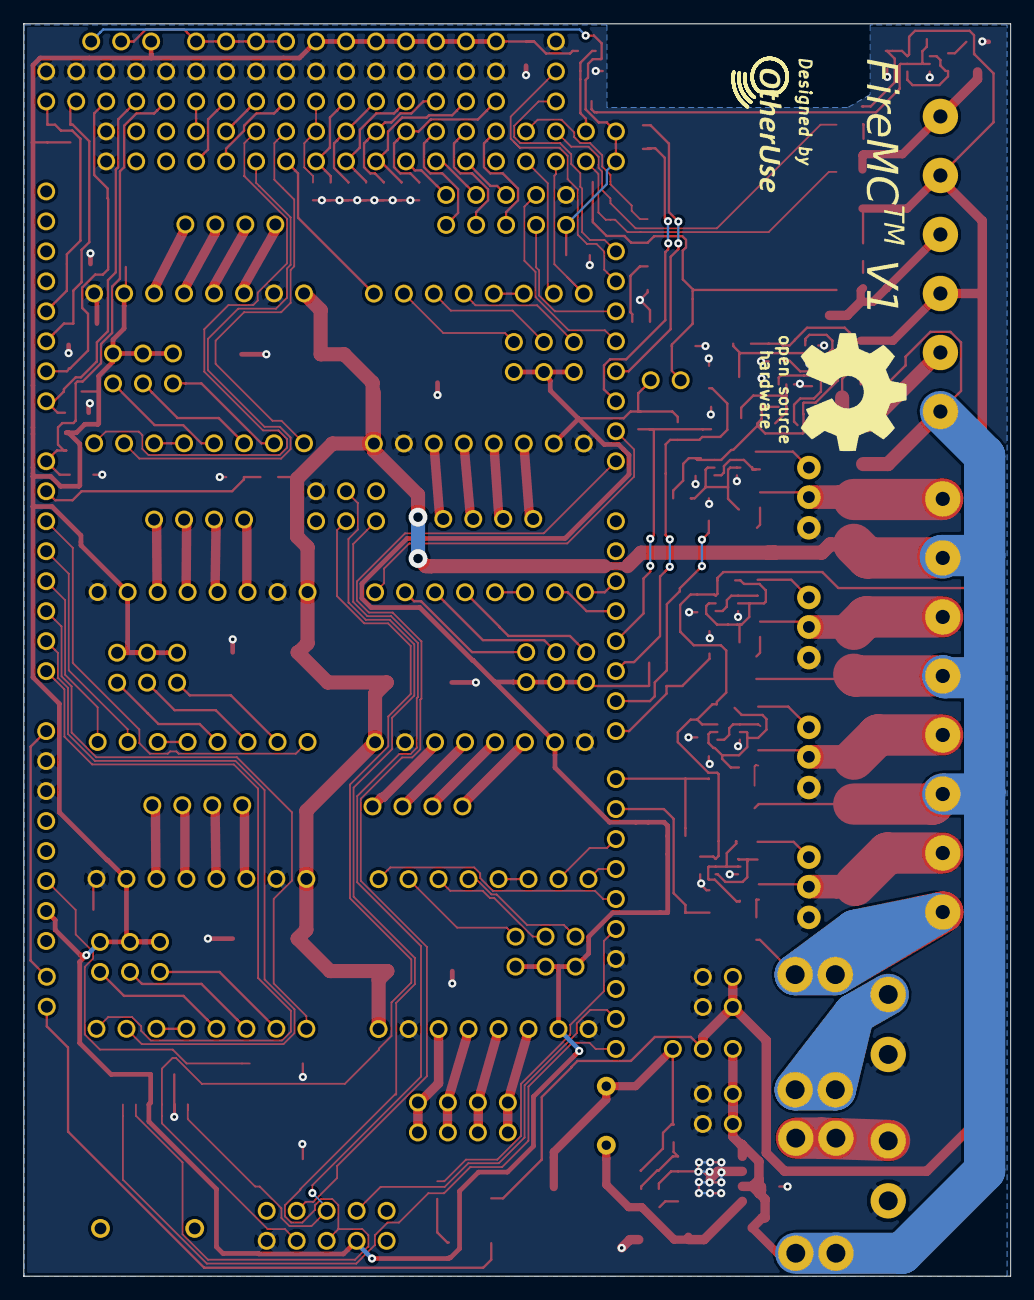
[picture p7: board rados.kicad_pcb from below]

Board: 2 copper layers, 83.6 x 106.1 mm, 166 parts (2 on the bottom side), 166 nets.

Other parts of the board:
JP2: CONN_01X02; CON_HDR_1x2_2.54mm
svg2mod, svg2mod#2: G***; firemc-logo
svg2mod#3: G***; OtherUseLogo_medium

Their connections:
ARDUINO-VIN: JP2.2; also elsewhere on the board
unnamed 50: JP2.1; also elsewhere on the board

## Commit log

2016-01-05 RADOS initial version
    [misc.sch, mosfets.sch, power.sch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]
2016-01-06 more schematics
    [misc.sch, mosfets.sch, rados.kicad_pcb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]
2016-01-07 More schematics, some layout
    [misc.sch, mosfets.sch, power.sch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]
2016-01-11 more placement and routing
    [misc.sch, mosfets.sch, power.sch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]
2016-01-11 More routing
    [misc.sch, mosfets.sch, power.sch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]
2016-01-12 Routing almost finished
    [misc.sch, rados (copy).kicad_pcb, rados.kicad_pcb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]
2016-01-13 Added 3d models
    [misc.sch, mosfets.sch, power.sch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]
2016-01-15 More 3d stuff
    [misc.sch, mosfets.sch, power.sch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]
2016-01-16 fixed minor issue
    [misc.sch, mosfets.sch, power.sch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]
2016-01-17 fixed some errors
    [mosfets.sch, rados.kicad_pcb, rados_union.FCStd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]
2016-01-21 Silkcscreen placement
    [rados.kicad_pcb]
2016-02-10 - added wifi esp8266 - switched caps to smd - fixed dual transistor pinout bug
    [misc.sch, mosfets.sch, power.sch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]
2016-02-11 Lots of routing
    [rados.kicad_pcb]
2016-02-11 some refinements
    [misc.sch, rados.kicad_pcb]
2016-02-12 Replaced SMPS with ST ic
    [power.sch, rados.kicad_pcb, rados.sch]
2016-02-12 Silk placement
    [rados.kicad_pcb]
2016-02-13 Moved heatbed io away from arduino led-output (D13)
    [rados.kicad_pcb, rados.sch]
2016-02-15 - Some mosfets now can have hardware PWM - moved eeprom to i2c with arduino pull-ups
    [misc.sch, rados.kicad_pcb, rados.sch]
2016-02-16 Fixed some TODO's
    [misc.sch, rados.kicad_pcb, rados.sch]
2016-02-18 Added minimal arduino mega support
    [misc.sch, mosfets.sch, power.sch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]
2016-02-19 Added some names/logo's on silkscreen
    [rados.kicad_pcb]
2016-02-19 Renamed schematics
    [misc.sch, mosfets.sch, power.sch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]
2016-02-22 Changed gate resistor values
    [mosfets.sch]
2016-03-08 Added component specifications
    [misc.sch, mosfets.sch, power.sch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]
2016-03-10 Added specifications and manufacturers to component attributes
    [misc.sch, mosfets.sch, power.sch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]
2016-03-10 More specs
    [power.sch]
2016-03-17 - Fix si2318 pinout - Fix slot problem introduced with attribute changes
    [mosfets.sch, power.sch, rados.kicad_pcb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]
2016-03-18 Clearance around wifi power jumper
    [rados.kicad_pcb]
2016-03-24 fix analog and wifi
    [misc.sch, rados.kicad_pcb, rados.sch]
2016-03-24 Added logo's that somehow disappeared
    [rados.kicad_pcb]
2016-05-28 Removed jumper in arduino power line: arduino is now always powered when FireMC is powered
    [power.sch, rados.kicad_pcb]
2016-08-16 Rescued some symbols
    [misc.sch, mosfets.sch, power.sch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]

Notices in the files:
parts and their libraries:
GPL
